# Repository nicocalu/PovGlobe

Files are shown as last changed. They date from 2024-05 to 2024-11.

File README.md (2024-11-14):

# PovGlobe
Forked from : @rottaca

This project consists of a 3d printed persistence of vision (POV) globe which is able to render arbitrary spherical images from appliations, written in c++ or python.
I changed some parts of the code and some physical parts, to be able to use agile fabrication tools (laser and plasma cutting machines, bending presses, etc.)
I also made a poster in french explaining the mechanics and electronics of the device.

## Setup
- [Setup Instructions](doc/setup.md)

## Poster
Poster

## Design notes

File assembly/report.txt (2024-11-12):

Nom du rapport: \\unity-home.insa-lyon.fr\users\home\ncardenas\P2I\GLOBE\SolidEdge\report.txt
Heure du rapport: 01/06/2024 13:05:57
Options du rapport:
    Noms des pièces

Ensemble de sélection #1:
    brushBase.par:1

Interférences:
    1 de 3
    brushBase.par:1
    mot-xd-3240.par:1

    2 de 3
    brushBase.par:1
    BrushR.par:1

    3 de 3
    brushBase.par:1
    BrushR.par:1

    3 Interférences détectées

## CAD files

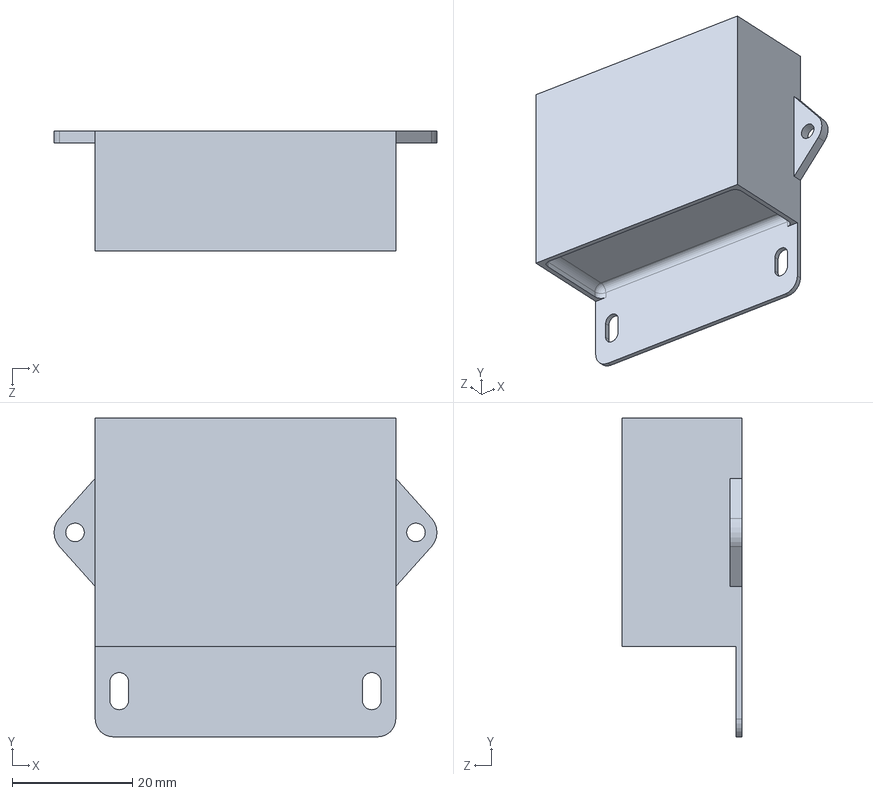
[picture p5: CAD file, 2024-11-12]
assembly/pieces/DCtoDC/MAIN BODY, DC TO DC CONVERTER, 12V OR 24V TO 5V, 10 AMPS, 50 WATTS, TOBSUN EA50-5V.SLDPRT
63.7 x 53.0 x 20.0 mm

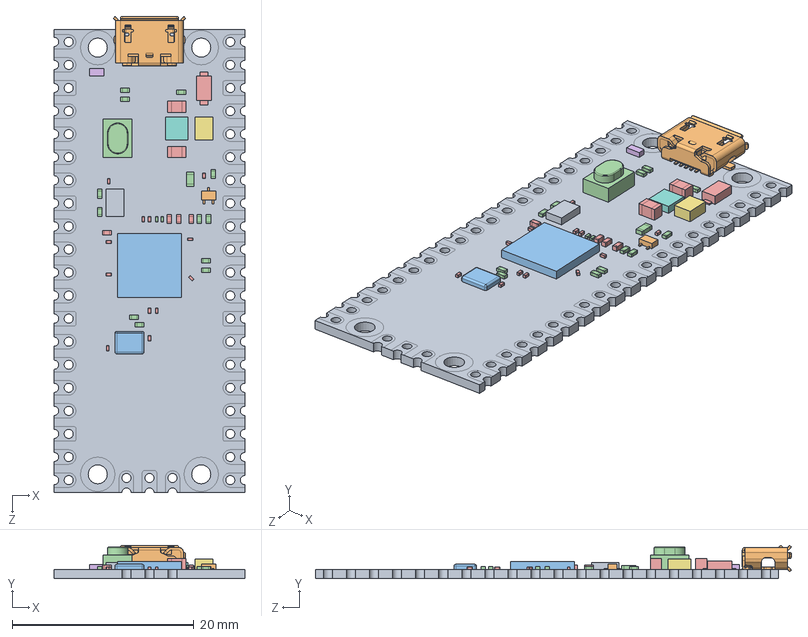
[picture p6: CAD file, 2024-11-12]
assembly/pieces/pipico/Raspberry Pi Pico-R3.SLDASM
21.0 x 3.69 x 52.4 mm
PCB, Raspberry Pi Pico-R3
MicroUSB Port, Raspberry Pi Pico-R3
RP2040 Microcontroller, Raspberry Pi Pico-R3
SW1, Tact Switch, Raspberry Pi Pico-R3
D1, Diode, Schottky, Raspberry Pi Pico-R3
D2, QSME-C194, LED, Raspberry Pi Pico-R3
L1, Inductor, Raspberry Pi Pico-R3
U2, RT6150B-33GQW, Buck Boost Converter, Raspberry Pi Pico-R3
U3, W25Q16JVUXIQ, Serial NOR Flash 16 Mbit, Raspberry Pi Pico-R3
Q1, MOSFET, DMG1012T, Raspberry Pi Pico-R3
X1, X12M000000S096, 12 Mhz Crystal Resonator, Raspberry Pi Pico-R3
SMD Resistor, Configurable, Raspberry Pi Pico-R3 x 15
SMD Capacitor, Configurable, Raspberry Pi Pico-R3 x 18

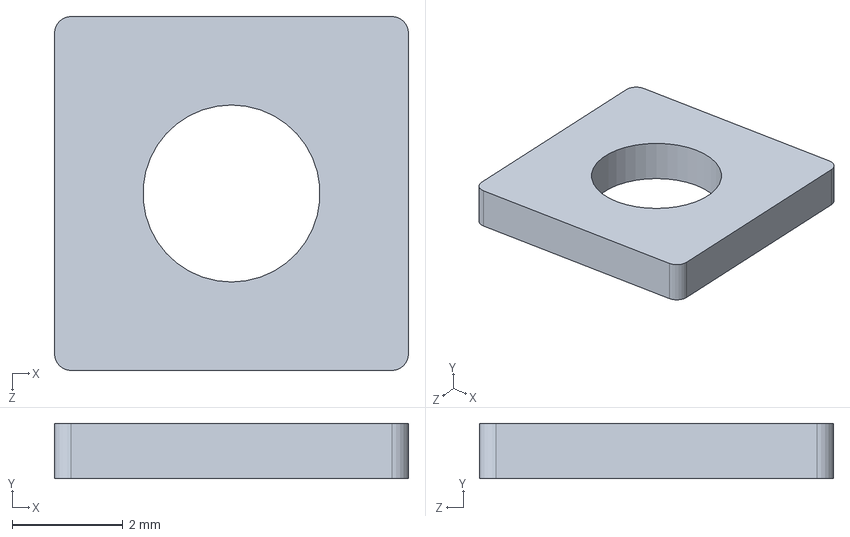
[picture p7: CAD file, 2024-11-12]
assembly/pieces/DCtoDC/WIRE CLAMPING PLATE, DC TO DC CONVERTER, 12V OR 24V TO 5V, 10 AMPS, 50 WATTS, TOBSUN EA50-5V.SLDPRT
6.40 x 1.00 x 6.40 mm

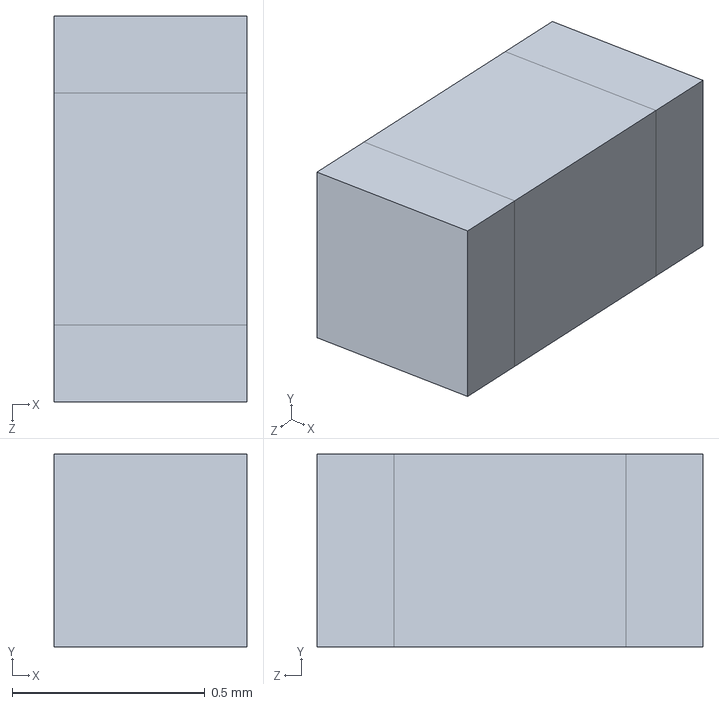
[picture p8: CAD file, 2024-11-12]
assembly/pieces/pipico/SMD Capacitor, Configurable, Raspberry Pi Pico-R3.SLDPRT
0.5 x 0.5 x 1.00 mm

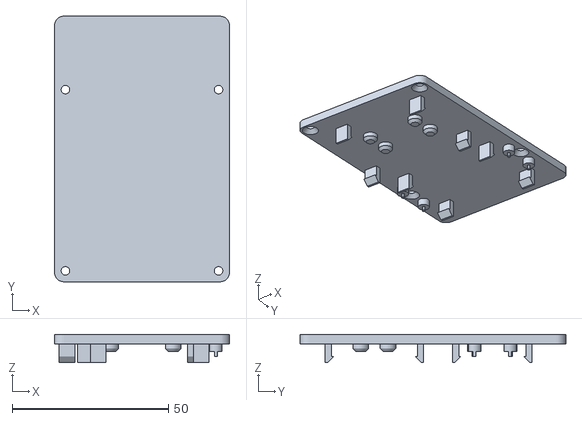
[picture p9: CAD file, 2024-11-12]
assembly/reference/pico_mount.stl
56.0 x 85.0 x 9.00

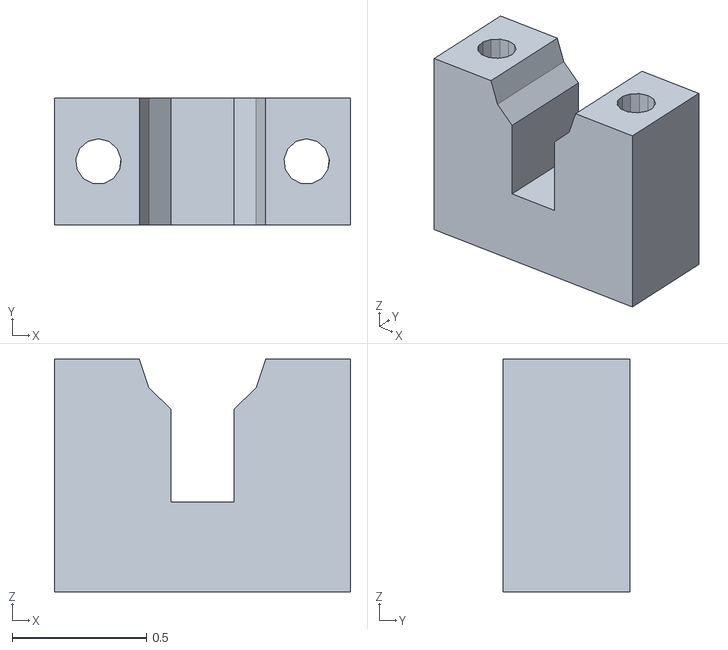
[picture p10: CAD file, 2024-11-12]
assembly/stl+tsk/globe_tite.stl
1.10 x 0.472 x 0.866

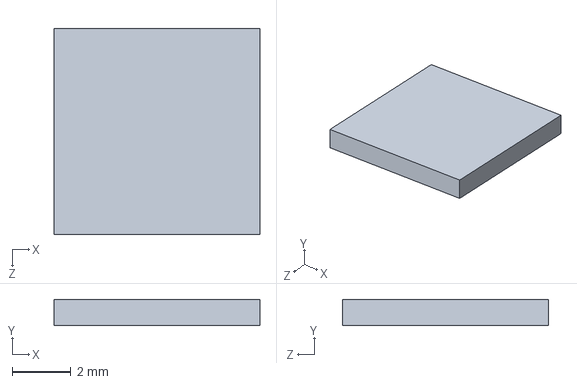
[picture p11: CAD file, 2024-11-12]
assembly/pieces/pipico/RP2040 Microcontroller, Raspberry Pi Pico-R3.SLDPRT
7.00 x 0.9 x 7.00 mm

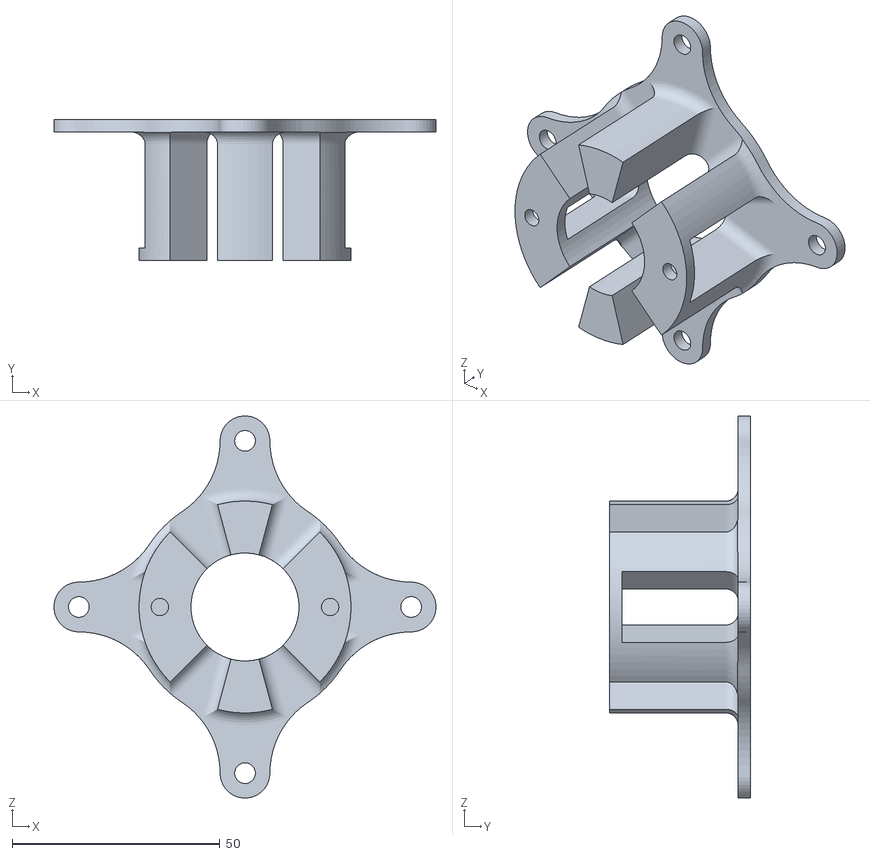
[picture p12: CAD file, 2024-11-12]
assembly/reference/motor_mount.stl
92.0 x 34.0 x 92.0

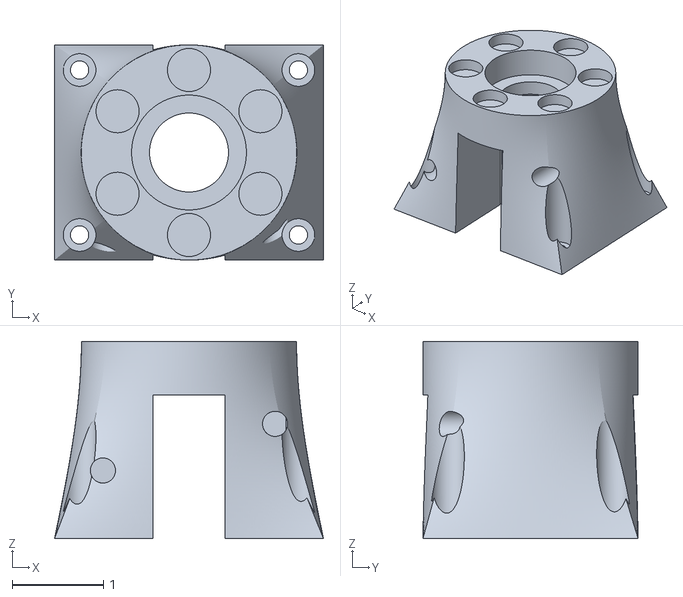
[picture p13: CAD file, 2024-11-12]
assembly/stl+tsk/brushBase.stl
2.95 x 2.36 x 2.17

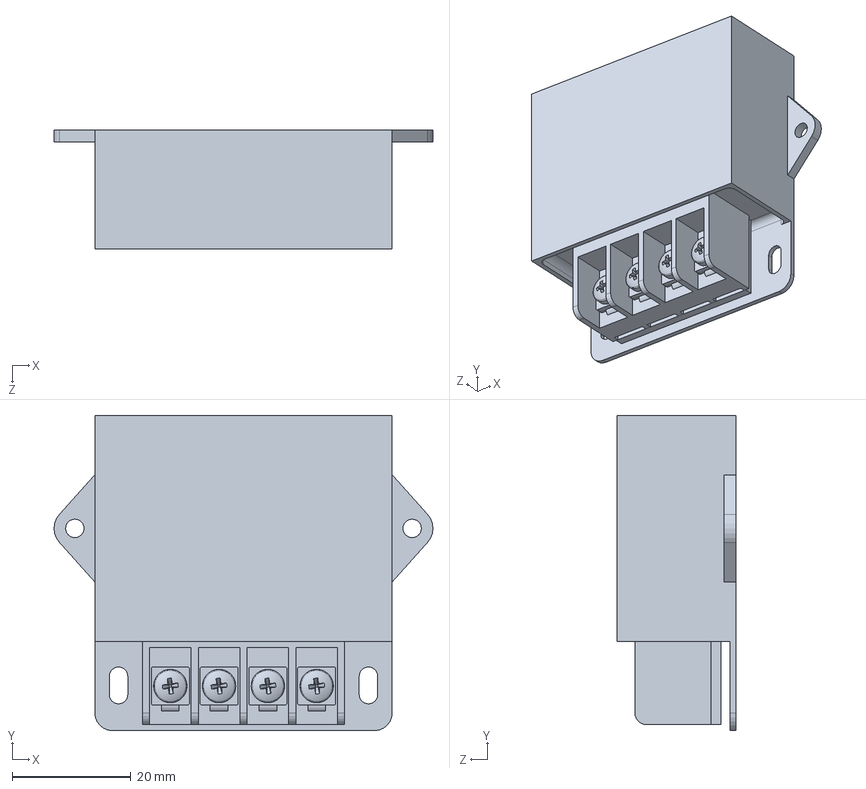
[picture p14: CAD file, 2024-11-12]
assembly/pieces/DCtoDC/DC TO DC.SLDPRT
63.7 x 53.0 x 20.0 mm

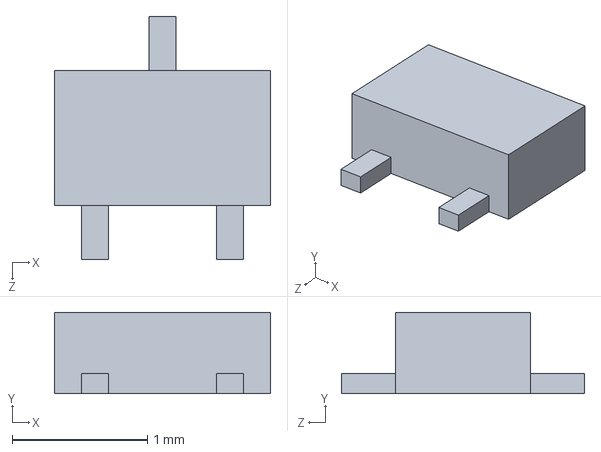
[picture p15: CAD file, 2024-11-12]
assembly/pieces/pipico/Q1, MOSFET, DMG1012T, Raspberry Pi Pico-R3.SLDPRT
1.60 x 0.6 x 1.80 mm

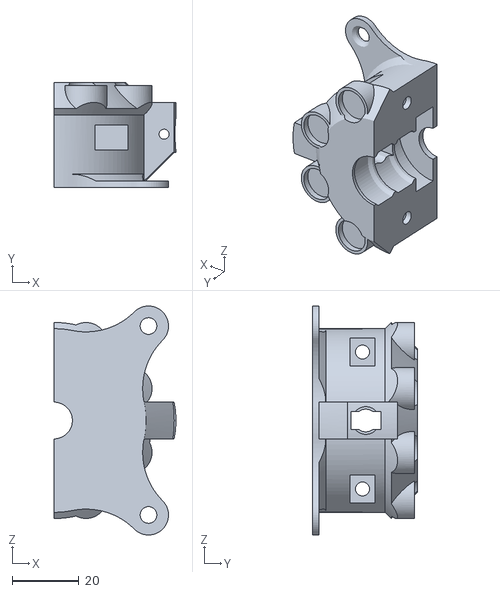
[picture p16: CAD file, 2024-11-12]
assembly/reference/power_transmition_part_1.stl
36.5 x 31.5 x 68.6

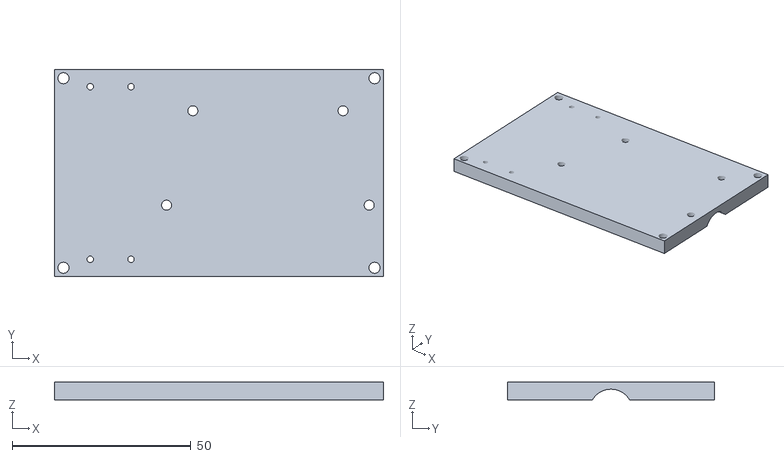
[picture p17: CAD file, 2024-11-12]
assembly/stl+tsk/supportPico.stl
92.0 x 58.0 x 5.00

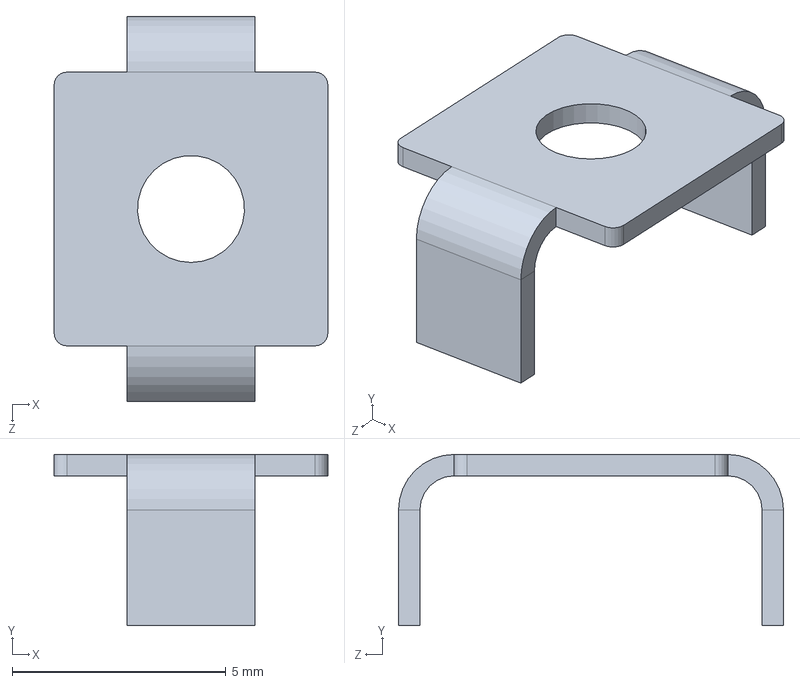
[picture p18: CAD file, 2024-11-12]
assembly/pieces/DCtoDC/TERMINAL PLATE, DC TO DC CONVERTER, 12V OR 24V TO 5V, 10 AMPS, 50 WATTS, TOBSUN EA50-5V.SLDPRT
6.40 x 4.00 x 9.00 mm

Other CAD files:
assembly/pieces/pipico/SMD Resistor, Configurable, Raspberry Pi Pico-R3.SLDPRT
assembly/reference/rotor_top_right.stl
assembly/stl+tsk/3dComm.stl
assembly/pieces/DCtoDC/DC TO DC CONVERTER, 12V OR 24V TO 5V, 10 AMPS, 50 WATTS, TOBSUN EA50-5V.STEP
assembly/pieces/DCtoDC/DC TO DC CONVERTER, 12V OR 24V TO 5V, 10 AMPS, 50 WATTS, TOBSUN EA50-5V.SLDASM
assembly/pieces/DCtoDC/DC TO DC CONVERTER, 12V OR 24V TO 5V, 10 AMPS, 50 WATTS, TOBSUN EA50-5V.x_b
assembly/pieces/DCtoDC/TERMINAL BLOCK, DC TO DC CONVERTER, 12V OR 24V TO 5V, 10 AMPS, 50 WATTS, TOBSUN EA50-5V.SLDPRT
assembly/pieces/pipico/D1, Diode, Schottky, Raspberry Pi Pico-R3.SLDPRT
assembly/pieces/pipico/D2, QSME-C194, LED, Raspberry Pi Pico-R3.SLDPRT
assembly/pieces/pipico/L1, Inductor, Raspberry Pi Pico-R3.SLDPRT
assembly/pieces/pipico/MicroUSB Port, Raspberry Pi Pico-R3.SLDPRT
assembly/pieces/pipico/PCB, Raspberry Pi Pico-R3.SLDPRT
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

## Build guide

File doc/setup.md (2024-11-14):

# Introduction
These setup instructions should enable you to build your own globe.

Please be adviced that signifficant knowledge about electronics is necessary in order to build this globe.
Also a good understanding of software development is necessary to implement new algorithms/visualizations.

Due to my limited time (:smile:), only basic documenation is available and you probably have to figure out some things on you own (mostly hardware related). If you worked on a similar project before, this should not be an issue for you!
There is a full wiring diagram in the KiCad folder, that can help you if you are having trouble with that.

## Part List
Several crutial parts are necessary to build this globe. Here is a list of the most important parts:
- Raspberry Pi 3 B+ or newer with standard os (e.g. ubuntu, no GUI required)
- DC motor, ~ 1200 RPM under load (results in up to 20 rotations per second, 20 FPS refresh rate)
  - I used this motor: www.amazon.de/gp/product/B0768DVMYN
  - I was not able to achieve these high rotation speeds because of vibrations and had to slow down the motor
  - Therefore I used an adjustable step-down converter to manually control the motor speed
- High density LED Strip with 144 LEDs/m
  - with APA102/SK9822 chips, **no WS28xx - their update rate is too slow!**
  - I used these: www.amazon.de/BTF-LIGHTING-ähnlich-Individuell-adressierbar-Nicht-wasserdichtes/dp/B07BPQV7FW
  - 
- Powersupply 24V (50-60W) depends on the number of LEDs and the motor
  - High voltage is necessary for power transfer with carbon brushes
  - I used something similar to this (mabye a bit overpowered): www.amazon.de/Docooler-100V-Spannungswandler-Schalter-Spg-Versorgungsteil/dp/B01LAVDD8S
- Carbon brushes to transfer electric power to the spinning globe 
  - I had some old ones laying around
  - The have to fit the 3d printed housing or you build your own
  - 5mm wide x 8mm high and 12mm long
  - Similar to this one www.amazon.de/vhbw-Kohle-Bürste-Motorkohle-Schleifkohle-Elektrowerkzeug/dp/B0799PMH36
- 6 Neodym Magnets (10 x 2 mm)
  -  www.amazon.de/gp/product/B06X977K8L
-  LM2596 DC-DC Buck Converter for converting the 24V into 5V for LEDs + RPi + Pico
   -  www.amazon.de/LAOMAO-Step-up-Converter-Raspberry-DIY-Projects-1-St%C3%BCck/dp/B00HV59922
- 3D printed parts 
  - All of these are in the pieces folder
- Wooden showcase with solid base (used as a housing for the globe)
  - 300 mm square base, >= 320mm height
  - I build my own base (140mm high) to hide the motor

# Software Setup
In order to build the software, provided in this repository, you need several software packages:

On Linux (Raspberry Pi):
- CMake (3.20.2): https://cmake.org/download/
```bash
sudo apt-get install cmake g++-4.8
```

### PICO SDK:
- https://datasheets.raspberrypi.com/pico/getting-started-with-pico.pdf (page 31)

- SWIG (4.0.2): http://swig.org/Doc4.0/SWIGDocumentation.html#Preface_unix_installation

- ImageMagick6 (6.9.12) https://legacy.imagemagick.org/script/download.php
```bash
sudo apt-get install libmagick++-dev
```

- bcm2835 library for raspberry pi: https://raspberry-projects.com/pi/programming-in-c/io-pins/bcm2835-by-mike-mccauley
  
- In order to use the python webserver, you have to install a few pip packages for python3.
```bash
py -3 pip -m install flask requests
```

## Configure Globe
The software has a set of configurable parameters in order to work with arbitrary globes (e.g. different number of LEDs). These settings have to be configured in two files (one for the rpi software and a second time for the pico).
- Raspberry Pi Software
  - The framework has two entrypoints. One for the c++ implementation and one for the python wrapper.
  - For the c++ implementation, the settings are set in `cpp_src\PovGlobe\main.cpp` lines 24-27.
  - For the python implementation, which includes the webserver, the same settings are hard-coded in `py_src\globe_wrapper.py` line 21-25.
  - Adjust the settings according to you needs. Here is a short description
    - leds = 55 -> 55 Pixels per side
    - radius = 13.25 -> Radius of the globe in centimeters
    - spacing_top = 1.5 -> How much is the last LED at the top away from the rotation axis. 1.5 cm by default.
    - spacing_bottom = 2.0 -> How much is the last LED at the bottom away from the rotation axis. 2 cm by default.
- The Pico Firmware
  - For the pico, the settings can be configured here: `pico_src\Renderer\constants.hpp` 
  - It has a lot more properties but most of them should stay unchanged unless you know what you are doing
  - Important parameters are:
    - N_VERTICAL_RESOLUTION -> Number of leds on one half of the globe (55 by default).
    - N_HORIZONTAL_RESOLUTION -> Number of "pixels" along the horizontal axis. This has to match the configuration of the rpi. The rpi software will determine this value, based on the given phisical dimensions of the globe. When running the rpi software, a summary of these calculated parameters will be printed. This can be used to configure the pico correctly. Picking the wrong value will not damage your pi or pico, but both components will detect the missmatch and no image gets displayed.
    - N_MAGNETS: Number of magnets, used for motion detection (8 by default and changing this might require adapting the code too)
    - The other settings include the pin layout of the pico which is used to communiate with the Rpi and to control its sensors and LEDs.

## Build Instructions

### Linux (Bash)
On linux, we can build the simulation environment, the hardware environment and the pico firmware. All will be build by the following command if all necessary dependencies are installed.
```bash
mkdir build
cd build
cmake ..
make -j4
```
Now, we have to flash the rpi pico firmware in order to get the globe running. This can be done by this script: `pico_src/flash.py`. Run it like this:

```bash
sudo py -3 pico_ src/flash.py <path-to-uf2-file-in-build>
```
The script will mount the pico, upload the firmware and unmount the pico again. After that, the firmware should be flashed.
**If your build fails, or has any compilation errors, I recommend you wipe your RPi and install the dependencies from scratch**

### Simulation
To make sure that the build was suceesfull, lets start with the simulation environment which renders the globe onto a window
on your monitor instead of using your hardware.

Executing the following command will launch two windows which show the globe surface as a 2D image and as a 3d sphere.
Running the command without arguments will use the compiled parameters, defined in main.cpp. They can be overwritten by 
the commandline arguments, listed below.
#### Linux
```bash
build/cpp_src/PovGlobe/Release/PovGlobe
```
#### Windows
```bash
.\build\cpp_src\PovGlobe\Release\PovGlobe.exe
```

You should see something like this:
```
--------------------- Globe Initialized --------------------
Globe Radius:                     13.25cm                                                                              
Num LEDs per side:                55                                                                                    
Num Pixels for half circle:       60                                                                                    
Num Pixels horizontal:            120                                                                                   
Leds are attached on both sides:  no                                                                                    
Spacing top    (cm / ratio in %): 1.5 cm (3.60351 %)                                                                    
Spacing bottom (cm / ratio in %): 2 cm (4.80468 %)                                                                      
No algo specified. Running default algo ApplicationTest1.                                                               
Initialize Renderer...                                                                                                  
Waiting for app to stop...                                                                                              
App stopped.                                                                                                            
Initialize Application...                                                                                               
[Render Thread]: Loop Time is avg 8.60606 ms, max 23 ms).                                                               
[Application Processing]: Loop Time is avg 9.88889 ms, max 50 ms).                                                      
[Render Thread]: Loop Time is avg 7.14141 ms, max 30 ms).                                                               
[Application Processing]: Loop Time is avg 19.9798 ms, max 50 ms).                                                      
[Render Thread]: Loop Time is avg 6.36364 ms, max 13 ms).                                                               
[Application Processing]: Loop Time is avg 30.1212 ms, max 52 ms).   
```

| Argument | Description |
|---|---|
| -a \<ALGO> | Specify the name of the algorithm you want to execute. The list is hardcoded in main.cpp. If not specified, the default test-app is launched. | 
| -f \<PATH> | Optional argument for some apps to specify a file path (e.g. which image to load). | 
| -h \<HEIGHT> | Number of pixels/LEDs used for the vertical dimension | 
| -r \<RADIUS> | Radius of the globe in centimeters, used in combination with -t and -b. This is used to correctly visualize which part of the globe is covered with LEDs. If you don't care, leave it unchanged during simulation but make sure its correct when using the hardware in order to avoid image distortions. | 
| -t \<SPACING> | Spacing from the upper end of the veritcal axis to the first led in centimeters, used in combination with -r and -b. | 
| -b \<SPACING> | Spacing from the bottom end of the veritcal axis to the first led in centimeters, used in combination with -r and -t. | 
| -d | Your globe has LEDs on BOTH sides of the rotator. Only relevant for hardware rendering. | 
| -k | If specified, the globe is using the hardware instead of the simulation environment. | 
--------

For example you can simulate a high-resolution globe, visualizing a custom image by executing:
```bash
PovGlobe -h 512 -a ImageViewer -f my_img.png
```

### Hardware-Test
A first test is to run the Pico firmware by itself. Only connect the pico to the LED strip and the hall sensor and rotate the globe. On boot up, the Pico will draw a few simple visualizations and then waits for the Raspberry Pi to take over control.

If this test is successful, we can continue using the Raspberry Pi. Make sure you were able to succesfully build the software by following the steps above, labeled "Build Instructions".

To make things easy, you can start by executing the core framework itself (without the python wrapper and the webserver). Take a look at the instrictions in the "Simulation" section above.
By passing "-k" to the PovGlobe executable, the globe will use the available hardware to visualize the image. In order to access the hardware we need sudo rights:
#### Linux (no hw support on windows)
```bash
sudo build/cpp_src/PovGlobe/Release/PovGlobe -h <NUM_LEDS> -k
```

### Webserver
If that is successful, you can give the webserver a try. It is located in **\<ROOT>/py_src/**.
Open the file globe_wrapper.py and adjust the settings if needed (starting from line 20):
```python
num_leds_per_side = 55
radius = 13.25
spacing_top = 1.5
spacing_bottom = 2.0
double_sided = True
```

By default, the webserver will start with hardware support when it detects a linux operating system.
This can be overwritten by modifying this line:
```python
usw_hw = not running_windows
```
After you are done with configuration, we can start the webserver by executing:
```python
sudo -E python3 /home/pi/PovGlobe/py_src/app.py
```
You should see something like this:
```
--------------------- Globe Initialized --------------------
Globe Radius:                     13.25 cm
Num LEDs per side:                55
Num Pixels for half circle:       60
Num Pixels horizontal:            120
Leds are attached on both sides:  yes
Spacing top    (cm / ratio in %): 1.5 cm (3.60351 %)
Spacing bottom (cm / ratio in %): 2 cm (4.80468 %)
Initialize Renderer...
Waiting for app to stop...
App stopped.
Initialize Application...
 * Serving Flask app "app" (lazy loading)
 * Environment: production
   WARNING: This is a development server. Do not use it in a production deployment.
   Use a production WSGI server instead.
 * Debug mode: off
 * Running on http://0.0.0.0:5000/ (Press CTRL+C to quit)
[Render Thread]: Loop Time is avg 6.53535 ms, max 16 ms).
[Application Processing]: Loop Time is avg 9.74747 ms, max 46 ms).
[Render Thread]: Loop Time is avg 9.76768 ms, max 21 ms).
[Application Processing]: Loop Time is avg 20.0202 ms, max 49 ms).  
```
Check if you are able to open the webinterface by using a browser to navigate to *http://localhost:5000*. 
Replace "localhost" with the ip adress of your host if you open the browser on a different machine.

## Crontab
After building the source code, install a job in crontab to auto-start the app when the RPI boots up.
```bash
@reboot sleep 20 && sudo -E python3 /home/pi/PovGlobe/py_src/app.py > /home/pi/PovGlobe/log.txt
```

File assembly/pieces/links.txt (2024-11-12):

dc-dc converter: (20e)
https://www.amazon.de/-/en/Step-Down-Converter-SUPERNIGHT-Supply-Transformer/dp/B07XRRYWM1/

leds: (40e)
https://www.amazon.de/BTF-LIGHTING-%C3%A4hnlich-Individuell-adressierbar-Nicht-wasserdichtes/dp/B07BPQV7FW

motor: (~30e)
https://www.amazon.de/gp/product/B0768DVMYN

power: (20e)
https://www.amazon.de/Docooler-100V-Spannungswandler-Schalter-Spg-Versorgungsteil/dp/B01LAVDD8S

brushes: (10e)
https://www.amazon.de/vhbw-Kohle-B%C3%BCrste-Motorkohle-Schleifkohle-Elektrowerkzeug/dp/B0799PMH36

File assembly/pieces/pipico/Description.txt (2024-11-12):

Raspberry Pi Pico-R3

Link to CAD models:
https://grabcad.com/library/raspberry-pi-pico-r3-1

The first micro controller offered from the Raspberry Pi foundation. 

The software support and documentation are solid.  I will try to use it in a few projects.
https://www.raspberrypi.org/products/raspberry-pi-pico/

It's nice that it is programmable in both MicroPython and C++.
MicroPython files can be dragged and dropped to work right away, but I'm not sure if the same can be done for C/C++ files.

I was hoping for better deep sleep currents and idle power usage and also WiFi like the ESP32. Also a USB Type C connector in 2021 would have been nice.

I hope they take inspiration from the Tiny Pico (low power usage ESP32) and its good low power features.

https://www.tinypico.com/

#CAD #SolidWorks #3dmodel #microcontroller #raspberrypipico

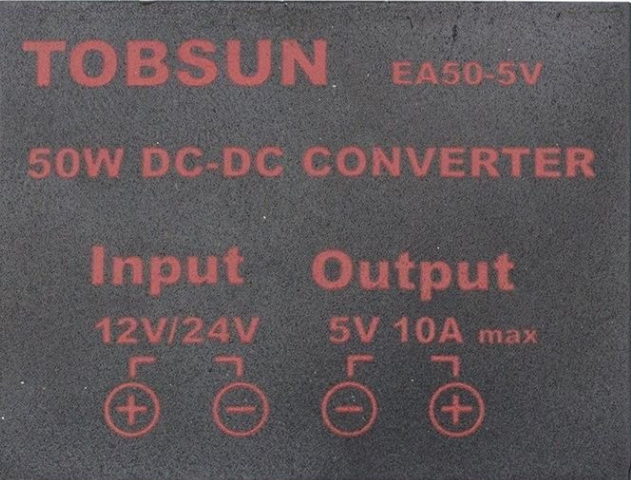
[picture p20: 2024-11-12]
assembly/pieces/DCtoDC/TOP IMAGE, DC TO DC CONVERTER, 12V OR 24V TO 5V, 10 AMPS, 50 WATTS, TOBSUN EA50-5V.PNG

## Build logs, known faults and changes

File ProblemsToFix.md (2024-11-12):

### 3d base for brushes:

- interference between the top of the motor and this part (motor has a round extrusion at the top), fixed by melting and adjusting the print.
- very tight space for mounting the brushes (but its doable)
- no space for the brush spring (diameter bigger than the carbon)
- the height of this part makes it necessary to cut the motor shaft to allow the cables to pass before the ball bearing (depends on the motor that you buy)

### axe:

- has to be done professionally: concentric and correct diameter. (or you can buy a premade Al tube extrusion).

### RPico plate:

- the holes in the Pico do not line up on the major axis.

### construction:

- difficult but possible to assemble the motor assembly (sheet base, motor and brushbase) (because having to tighten nuts in tight spaces).

### commutator assembly:

- fit too tight on shaft, need more clearance.
- redesign to not have to solder the wires to the copper, and just use an interference fit.

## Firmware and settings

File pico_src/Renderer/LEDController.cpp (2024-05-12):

#include "LEDController.hpp"

#include "pico/time.h"

#include "apa102.pio.h"
#include "RTTMeasure.hpp"

PIO LEDController::pio{};
uint LEDController::sm = 0;
uint8_t LEDController::pixel_buffer[2][N_BUFFER_SIZE];
mutex_t LEDController::mutex = {};
uint8_t LEDController::render_buffer_idx = 0;

LEDController::LEDController()
{
    mutex_init(&mutex);
    multicore_launch_core1(&LEDController::core1_write_pixels);
}

LEDController::~LEDController()
{
}

LEDController &LEDController::getInstance()
{
    static LEDController instance;
    return instance;
}

inline void LEDController::put_start_frame(PIO pio, uint sm)
{
    pio_sm_put_blocking(pio, sm, 0u); //4 bytes of zeroes
}

inline void LEDController::put_end_frame(PIO pio, uint sm)
{
    pio_sm_put_blocking(pio, sm, ~0u); //4 bytes of ones
}

inline void LEDController::put_rgb888(PIO pio, uint sm, uint8_t r, uint8_t g, uint8_t b)
{
    pio_sm_put_blocking(pio, sm,
                        0x7 << 29 |                     // magic
                            (BRIGHTNESS & 0x1f) << 24 | // global brightness parameter (5 bits 0-31)
                            (uint32_t)b << 16 |
                            (uint32_t)g << 8 |
                            (uint32_t)r << 0);
}

void LEDController::core1_write_pixels()
{
    pio = pio0;
    sm = 0;
    uint offset = pio_add_program(pio, &apa102_mini_program);
    apa102_mini_program_init(pio, sm, offset, LED_SERIAL_FREQ, LED_PIN_CLK, LED_PIN_DIN);

    RTTMeasure &rttMeasure = RTTMeasure::getInstance();
    LEDController &ledController = getInstance();

    ledController.put_start_frame(pio, sm);
    for (int i = 0; i < 2*N_BUFFER_SIZE_PER_COLUMN; i += N_CHANNELS_PER_PIXEL)
    {
        ledController.put_rgb888(pio, sm,
                                    0,  //render_buff[column * N_BUFFER_SIZE_PER_COLUMN + i],
                                    0,  //render_buff[column * N_BUFFER_SIZE_PER_COLUMN + i + 1],
                                    0   //render_buff[column * N_BUFFER_SIZE_PER_COLUMN + i + 2]
                                );
    }
    ledController.put_end_frame(pio, sm);
    
    uint32_t last_column = 0xFFFFFF;
    uint32_t column, opposite_column;
    while (true)
    {
        const absolute_time_t curr_time = get_absolute_time();
        rttMeasure.getCurrentColumn(curr_time, column, opposite_column);  
        if (column != last_column){
            mutex_enter_blocking(&mutex);
            const uint8_t *render_buff = ledController.getRenderBuffer();

            ledController.put_start_frame(pio, sm);
            for (int i = 0; i < N_BUFFER_SIZE_PER_COLUMN; i += N_CHANNELS_PER_PIXEL)
            {
                ledController.put_rgb888(pio, sm,
                                            render_buff[column * N_BUFFER_SIZE_PER_COLUMN + i],
                                            render_buff[column * N_BUFFER_SIZE_PER_COLUMN + i + 1],
                                            render_buff[column * N_BUFFER_SIZE_PER_COLUMN + i + 2]
                                        );
            }
            for (int i = (N_VERTICAL_RESOLUTION - 1) *N_CHANNELS_PER_PIXEL; i >= 0; i -= N_CHANNELS_PER_PIXEL)
            {
                ledController.put_rgb888(pio, sm,
                                            render_buff[opposite_column * N_BUFFER_SIZE_PER_COLUMN+i ],
                                            render_buff[opposite_column * N_BUFFER_SIZE_PER_COLUMN+i + 1],
                                            render_buff[opposite_column * N_BUFFER_SIZE_PER_COLUMN+i + 2]
                                        );
            }
            ledController.put_end_frame(pio, sm);
            mutex_exit(&mutex);
            
            last_column = column;
            sleep_us(100);
        }
        else if (SHOW_DOT_MATRIX_STYLE) {
            ledController.put_start_frame(pio, sm);
            for (int i = 0; i < 2*N_BUFFER_SIZE_PER_COLUMN; i += N_CHANNELS_PER_PIXEL)
            {
                ledController.put_rgb888(pio, sm, 0, 0, 0);
            }
            ledController.put_end_frame(pio, sm);
        }
    }
}

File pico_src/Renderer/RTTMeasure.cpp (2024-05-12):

#include <stdio.h>
#include <cmath>

#include "RTTMeasure.hpp"

uint32_t RTTMeasure::m_measured_intervals[N_MAGNETS] = {};
int8_t RTTMeasure::m_curr_segment_index = 0;
critical_section_t RTTMeasure::critical_section = {};
absolute_time_t RTTMeasure::m_last_hall_sensor_event = nil_time;
absolute_time_t RTTMeasure::m_last_print = nil_time;

RTTMeasure::RTTMeasure()
{
    init();
    gpio_set_irq_enabled_with_callback(PIN_HALL_SENSOR, GPIO_IRQ_EDGE_RISE, true, &RTTMeasure::gpio_hall_sensor_callback);
    //set interrupt to callback func gpio_hall_sensor_callback
}

RTTMeasure::~RTTMeasure()
{
}

void RTTMeasure::init(){
    for (size_t i = 0; i < N_MAGNETS; i++)
    {
        m_measured_intervals[i] = get_absolute_time();
    }
    m_curr_segment_index = 0;
    m_last_hall_sensor_event = nil_time;

    critical_section_init(&critical_section); //set up critical section 
}

RTTMeasure& RTTMeasure::getInstance() {
    static RTTMeasure instance;
    return instance;
}

void RTTMeasure::gpio_hall_sensor_callback(uint gpio, uint32_t events) {
    const absolute_time_t curr_time = get_absolute_time();

    if (gpio != PIN_HALL_SENSOR)
        return;
    
    const uint32_t old_dt = m_measured_intervals[m_curr_segment_index];

    critical_section_enter_blocking(&critical_section);

    if (!is_nil_time(m_last_hall_sensor_event)){ //set up dts for the first time
        const uint32_t new_dt = absolute_time_diff_us(m_last_hall_sensor_event, curr_time);
        m_measured_intervals[m_curr_segment_index] = 0.5* new_dt + 0.5*old_dt;
    }
    m_last_hall_sensor_event = curr_time;
    m_curr_segment_index = (m_curr_segment_index + 1U) % N_MAGNETS; //change segment index
    critical_section_exit(&critical_section);
}
